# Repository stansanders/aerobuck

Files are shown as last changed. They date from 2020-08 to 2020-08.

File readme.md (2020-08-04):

# aerobuck

A free/libre open source aeroponic plant propagation tool designed to utilize a standard 5-gallon bucket to realize a system which is efficient in use and construction.

## Overview

The aim of this design is to improve on existing plant cloner designs in the following areas:   
 
* Cost: Require a minimal bill of materials  
* Leaks: prevent liquid escape completely, without complicated sealing efforts seen in many bin-based designs.  
* Simplicity: use no tools other than a printer and human hands  

This repository will provide the design files in STEP form to allow the design to be modified to suit the user, as well as STL files to provide a simple route for users to print the design as-is with no need to utilize a computer beyond providing the file to their printer.

## Bill of Materials  

* [printed manifold](aerobuck_manifold.stl)  
* [printed lid](aerobuck_lid.stl)  
* six (6) 360 degree 10-32 / M5-0.8 sprayer nozzles (botanicare micro sprayer, xGarden mister, etc) 
* 5 gallon bucket  
* 48mm neoprene cloner collars (commercially available or self made)
* submersible pump with 1/2" female threaded  upwards-facing outlet (ecoplus 396 has been tested, others may work as well)

## Printing recommendations

The manifold and lid designs have been tested using a modified version of the Voron v1.5 coreXY printer design, using Inland brand PLA+.  Most printers should be capable of printing the design adequately so long as their work envelope permits.  Slicer settings are left as an exercise to the user due to the wide variations in printer needs and plastic types.  A high number of perimeter shells, high infill percentage, and high number of top and bottom solid layers are a good idea due to the pressures and liquids involved.  Low quality prints may function for some time but should be observed for leaks in the manifold due to delamination and undesired liquid intrusion into the interior of the printed lid.  The test unit has a layer height of 0.2mm, 4 perimeter shells, 3 bottom solid layers, and 6 top solid layers.    

## Assembly
The manifold is designed as a single part which should thread into the submersible pump's outlet and form a good seal.  The holes in the upper surface of the manifold ring are sized to allow the sprayer nozzles to self-tap slightly.  A firm grip should be all that is needed, however allowing the plastic to warm either by sunlight or source of warm air (e.g. blow dryer) may ease the process.

With the nozzles fitted assembly is completed by threading the manifold into the pump, placing the pump and manifold assembly in the bucket such that the manifold ring is roughly centered, and setting the lid into the bucket with the neoprene collars fitted.

## Use
Cuttings should be of good health and cut with sharp tools shortly before insertion into the system.  The pump should run at all times and the reservoir should be kept full enough to cover the pump inlet with clean water.  A fungal control formula is outlined below and recommended to avoid cutting loss due to rot.  The system may be run indoors or outdoors so long as temperatures remain moderate and sunlight exposure is not excessive - system has been tested outdoors successfully in an area that receives approximately 2 hours of full direct sun and 10 hours of open shade.  Cuttings should require no further care until their root systems are sufficient to transplant to their final growing media.

This system has been tested and successful with cuttings of papayas (*Carica papaya*),  figs (*Ficus carica*), and tomatoes (*Solanum lycopersicum*).  Rooting has happened much more quickly and with less damage than other methods.  Many other species should also work well.

## Fungal Control

While not a part of the hardware design, fungal destruction of plant stems in this type of system is a primary cause of cutting loss so it is important to discuss ways to mitigate that issue.  Commercial solutions exist to address the problems one is likely to encounter however their cost is high compared to the formula below.

*Please exercise the appropriate precautions when handling potentially harmful materials.  Use appropriate safety equipment, follow appropriate safety procedures, observe all precautions specified by the relevant materials safety and data sheets.* 

Calcium hypochlorite is marketed for use in swimming pools and can be purchased cheaply.  "HTH 52023 Super Shock Treatment Swimming Pool Chlorine Cleaner" has been tested to work well and is readily available.  Other options should work well so long as they are of comparable composition.

Using calcium hypochlorite 56.44% in granular form, a stock solution is made by adding 0.26 grams of granules to 1 liter of plain water.  This stock solution is added to the cloner at a rate of 1.5 milliliters stock solution per liter of plain water.  For this design, 15 milliters of calcium hypochlorite stock solution and 10 liters of plain tap water should result in the water level being just below the sprayers.

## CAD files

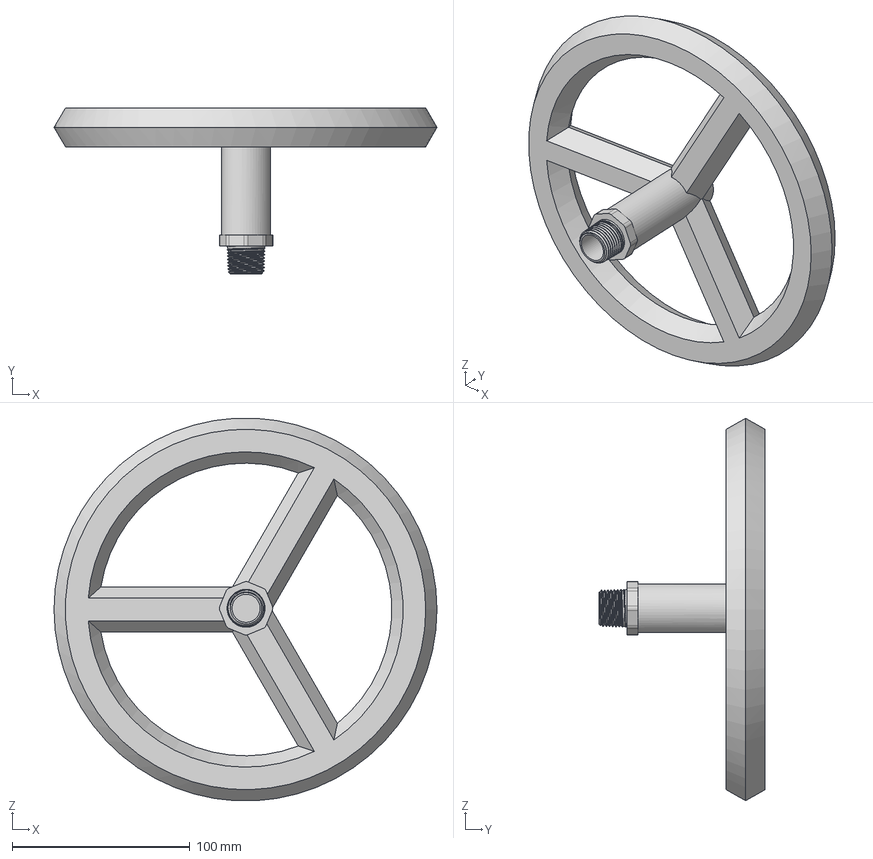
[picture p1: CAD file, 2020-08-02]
aerobuck_manifold.step
215.4 x 93.6 x 215.1 mm

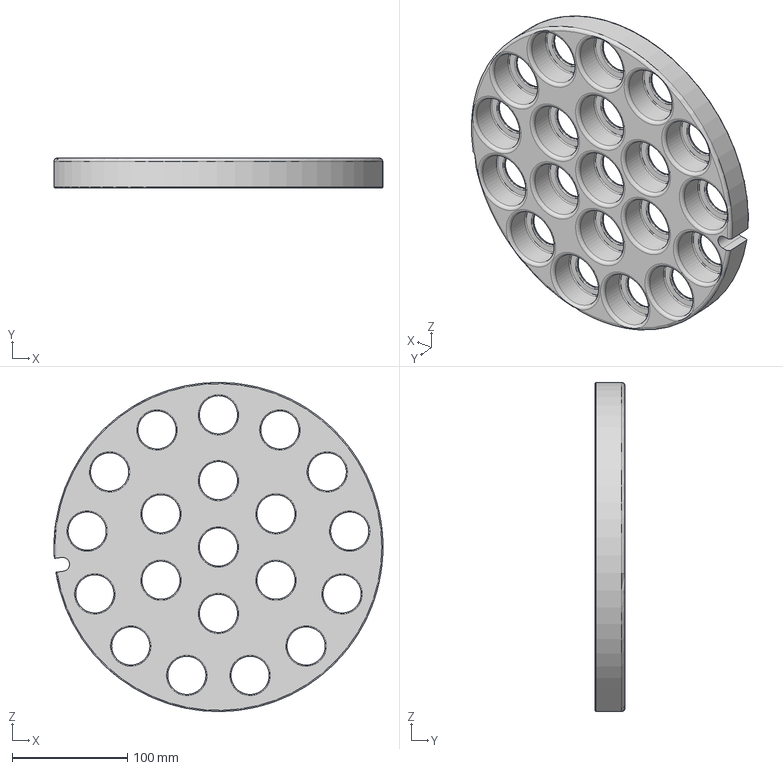
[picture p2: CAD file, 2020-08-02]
aerobuck_lid.step
284.9 x 26.0 x 285.0 mm

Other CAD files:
aerobuck_manifold.stl
